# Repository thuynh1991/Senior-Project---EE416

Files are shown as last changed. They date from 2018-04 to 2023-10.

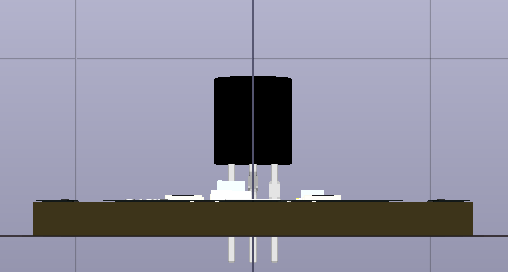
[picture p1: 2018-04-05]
Arduino_Nano_Shield_pics/3D_back.PNG

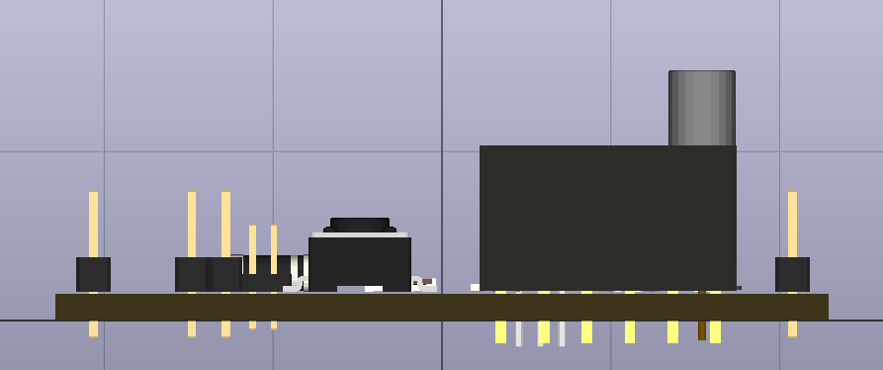
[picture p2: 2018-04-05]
Onboard System_pics/3D_back.PNG

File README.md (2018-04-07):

# Senior-Project---EE416: Leak Detection System for the Robosub Autonomous Submarine
Ensuring the protection of electronics is an integral portion of any electromechanical system. Our project goal is to protect electronics within the hull of the WSU Robosub Club’s autonomous submarine, by implementing methods of leak detection. Providing information of an onboard leak allows for preventative action, and could potentiallysave thousands of dollars worth of material onboard. We have developed a two-part procedure to check, and monitor for potential leaks. This procedure consists of testing for leaks before the submarine is submerged, and is followed by an internal system that monitors water infiltration while underway. This project has met the needs and requirements set by our clients and stakeholders, while maintaining freedom of engineering design interpretation.<br /><br />
The DS_LC234X is FTDI - USB connector and we will use atmega1284P-AU chip for the project. <br />
EE415 code: Code to test the leak before submarine is submerged. <br />
EE416 code: Code for the internal(onboard) system. <br />  
Aruino Nano Shield: is our back up plan in case the internal system is fail.

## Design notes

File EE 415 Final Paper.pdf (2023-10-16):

## Team Naura NAVSEA Robosub Alpha Prototype Results

EE 415

## December 4, 2017

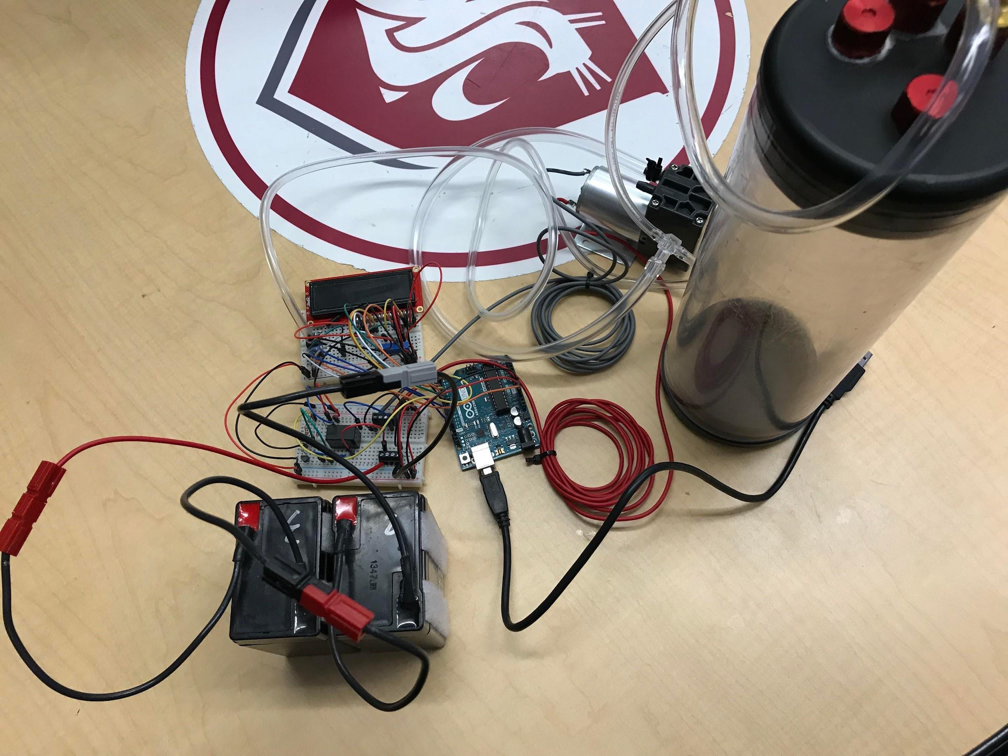
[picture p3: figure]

Mentors:
Aaron Darnton
Alex Read

Co-mentor:
Daniel Hubert

Faculty Volunteer:
Andy O’fallon

Professor:
Patrick Pedrow

Group Members:
Henderson Reaves
Nicholas Heitman
Luke Riske
Thong Huynh

Alpha Prototype Description

The objective for this semester was to develop a leak detection system for the Robosub club’s autonomous submarine, and present an alpha prototype model of the design to our industry mentors, and primary stakeholders involved. Our team followed an iterative design procedure until finally selecting a concept, and constructing the alpha prototype model. Our alpha prototype is defined as a pre-submergent leak detection system, which has been implemented by pulling a vacuum, and monitoring pressure differentials on a sealed vessel. The system is designed to require minimal human interaction, and provides clear and concise results. This scheme is standalone, and completely detached from the submarine while it is underway. Our team is confident this approach can also be useful on relative applications that need to be tested for airtightness.

Summary of Alpha Prototype Session with Industry Mentor

After introduction of ourselves, our alpha prototype model, industry mentors, and primary stakeholders to the attendees of our presentation; we began presenting on the development procedure of our alpha prototype. The following information is a summarization of the semester long iterative design process, and alpha prototype design details, which were covered in the alpha prototype presentation.

The first step in our design procedure revolved around establishment, and organization of our team. A group photo of our senior design team is shown in Figure 1, with corresponding names captioned below. The role of communication liaison for the fall semester was taken on by Nick Heitman. Our team assessed each other's strengths early on, and were able to conclude suitable roles for every member. Henderson Reaves, and Thong Huynh specialize in computer engineering, therefore, taking on tasks related with programming of the microcontroller. Luke Riske, and Nick Heitman are electrical engineers, and focused primarily on hardware design, and testing roles. Organization of tasks for each member were taken further by evaluating each other in networking, communication, research, and technical writing skills. Our team met frequently each week of the semester to update, and assess the iterative design procedure throughout the duration of EE415.

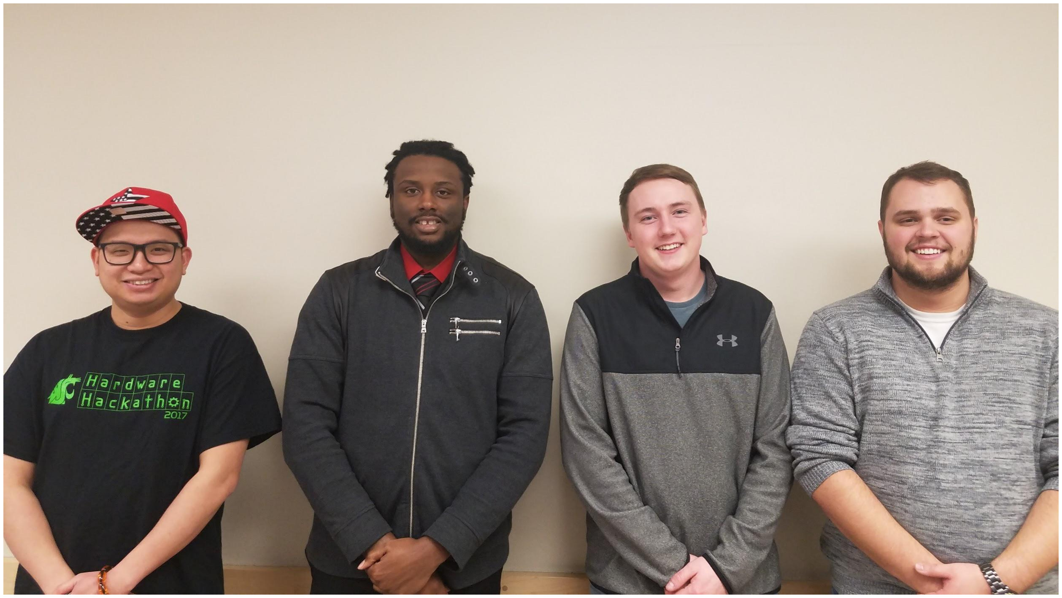
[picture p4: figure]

Figure 1. (From left to right): Thong Huynh, Henderson Reaves, Nick Heitman, and Luke Riske

It was crucial to develop an affirmative understanding of the design problem before defining goals, and specifications for our project. The abstract for the “Robosub” design problem influenced our team to interview the mentor’s from NAVSEA, and club members from Robosub to develop project needs. The summary of the problem also gave a clear indication that a pre-submersion, and internal leak detection system would be the primary focus of our design procedures. After consulting with our clients, it was clear that a water breach could damage thousands of dollars worth of electronics within the autonomous submarine, and their current method of leak detection was inefficient. Our team was able to extract needs for both systems through discussions with both parties. The information in Table 1 indicates the needs collected from meetings held with our NAVSEA mentors, and Robosub club leaders.

Table 1: Primary Needs for Pre-Submersion, and Internal Leak Detection Systems

Pre-Submersion System Needs | Internal System Needs
Minimal human interaction: Require low maintenance, and user inputs. | Send flag bit when hull is breached: Transfer data to the submarines AI system.
Display accurate and user friendly data: Show clearly whether the system is under passing or failing conditions. | Compatibility with their existing software: Must choose hardware that is programmable with their current software.
Quick results: Display test conditions in an acceptable timeframe. | Output to USB: Transfer data through their available ports.
Standalone from the AUV: Detachable, and portable system. | Meet available power requirements: Use their 12-14V onboard power supply.

The Robosub club suggested that our team keeps both systems separate, and focuses primarily on the pre-submersion system in the fall semester.

Before beginning the design phase, it is critical to work within the needs taken from clients, and stakeholders. In this situation it is the responsibility of the engineers to interpret the needs of the client into target technical specifications that can be designed around. The information contained in Table 2 shows the mapping of our clients’ needs into target technical specifications.
Table 2: Needs and Metrics with Ideal Margins
# | Need | Metrics (with ideal margins)

1 | External standalone functionality | Unit must have minimal user interfacing input, and low tolerance for data error (1 user input, 10% tolerance)
2 | Simple design | System that provides a relatively small footprint, and low maintenance (20 square centimeters)
3 | Pre-submergence check in timely manner | Check measurements, and conduct tests within a short period of time (Within 5 minutes)
4 | Meet available power specifications | Allow system to rely on independent power supply, without wall connection (12V-16V battery supply)
5 | Sampling time per measurement | Sample measurements at a fast pace (at least every 2 seconds)
6 | Accounting for changes of temperature that could be caused by internal electronics | Allow for fluctuations of temperature (2 degrees celsius)

Once, the target technical specifications were established, we had to consider the broader impacts that our design would have on surrounding systems, and the users of our design. To analyze the broader impacts we utilized the risk management technique, which was introduced by our instructor. There are 4 steps that must be followed to use this technique, which includes identifying risks, evaluating risks, making decisions, and reviewing the decisions. These steps pertain to our system design as follows in table 3.

Table 3: Risk Management technique for impact analysis

Step 1: Identify Risks | Step 2: Evaluate Risks | Step 3: Make Decision | Step 4: Review Decisions
Vacuum may drop the pressure too low | Loss: If the vacuum is overdrawn the test case could implode Probability: Low | Because it would take a very large pressure to implode the cases we moved forward with this decision | This decision was sound because controls restricting the vacuum were implemented
Board mount components may break | Loss: Components would need to be replaced Probability: Medium | Because this risk had a medium probability we continued forward with the decision but with extreme caution | This decision was questionable because we broke a leg off of the pressure sensor. Even though we fixed it.
Power supply could provide too much to the wrong place | Loss: Could cause component and system failure Probability: Low | Because we put protections in place to prevent this risk we moved forward with this decision | This decision was sound because preventative measures were taken
Numerous connections could present vulnerabilities | Loss: Could give inaccurate results Probability: Low | Because we could account for this in our tests we decided to move forward with this | This decision was sound because preventative measure were taken.

As indicated by Table 3, we were able to use the Risk Management technique to analyze the broader impacts of our system. Since these impacts were fairly low we proceeded forward with our design.

To generate concepts for the pre-submergent leak detection system we searched internally, and externally to develop possible solutions for each subsystem. The external searches included interviewing clients, and stakeholders; researching peer reviewed journal articles, searching patents, and benchmarking related products through the Thomas Register database. Some of the corresponding solutions to each subsystems are shown in Table 4.

Table 4: Concept Generation Table

Subsystems | Solution Concepts
Energy (Power) Supply | ● AC wall supply ● DC battery ● AC wall supply with rectifier circuit to convert DC ● Solar cell module ● Robosub submarine power supply ● Relay system between the “influence on vessel,” and “method of measurement subsystems” to centralize user input
Influence on Vessel | ● Removal of pressure from the vessel with vacuum generator ● Injection of pressure into the vessel with air compressor ● Injection of heat into the vessel with heating mechanism
Method of Measurement | ● Pressure measurement with pressure transducer ● Temperature measurement with temperature sensor ● Gas measurement with gas detector
Data Processing | ● PIC32 microcontroller ● Arduino based microcontroller ● FPGA ● Raspberry Pi ● Computer

In the concept selection process for the pre-submergent leak detection system, we evaluated each possible solution generated for each subsystem. Taking the Robosub club’s previous method of leak detection into account, which involved pulling a vacuum, and analyzing pressure differentials with an analog pressure gauge, we decided to follow a similar method by using a pressure sensor controlled with an arduino microcontroller. Since the design needed to be mobile, our team also concluded that a battery supply should be used to power our system. Addition of a relay was also considered to minimize human interaction, and add a safety element to our design. Table 5 shows the concept selection for our design.

Table 5: Concept Selection Table

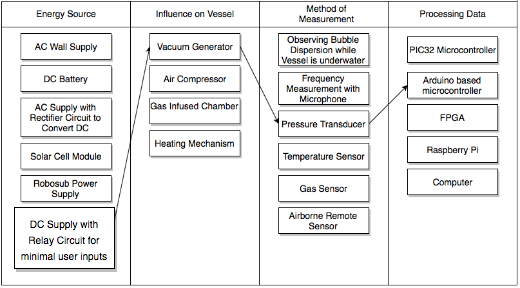
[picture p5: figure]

The initial hardware design we envisioned is shown in Figure 2, which involved connecting the microcontroller, and pressure sensor between the testing chamber with tubing. Turning on the vacuum generator would bring the combined volume to the same pressure level. Once the correct pressure level is reached the vacuum generator would be turned off by the relay, and the pressure sensor measures the pressure within the test chamber to make sure there is no major pressure deviations in a short timespan.

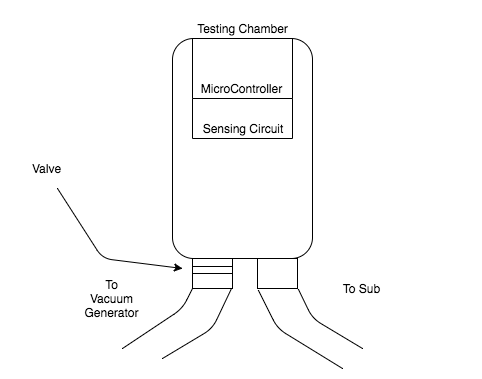
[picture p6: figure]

Figure 2. First Concept for the Pre-Submersion System

After looking further into our design, and pondering its abilities, we decided that the model was too bulky for transportion. The design was reconsidered to what is shown in Fig. 3, which consists of a ported pressure sensor connected directly with the vessel, and vacuum through tubing. This not only simplified the design, but allowed for the test chamber to simulate the submarine for the alpha prototype.

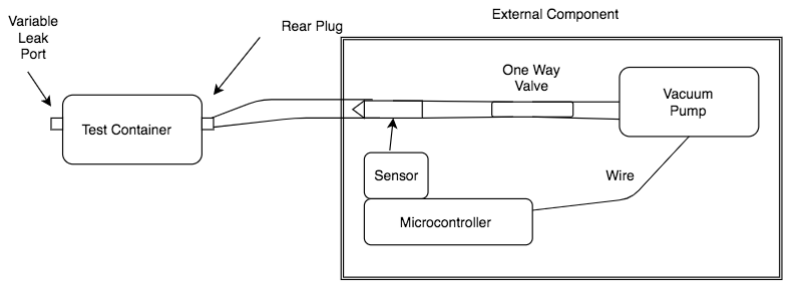
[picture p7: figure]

Figure 3. Second Concept for the Pre-Submersion System

Before our design could be built, we were obligated to contact the EHS regarding the safety of pulling a vacuum on a sealed vessel. We were assigned to complete a job hazard assessment EHS assistant director Shawn Ringo. The assessment was meant to identify potential hazards, appropriate controls, and personal protective equipment. Shortly after submission we were informed that our job hazard assessment was acceptable for the design.

The Arduino UNO microcontroller was borrowed from the Robosub club for this design, and is used for interfacing each of the subsystems within the pre-submergent leak detection system. The UNO serves as a placeholder in our alpha prototype for a printed circuit board in the future. After extensive research we determined the HSC differential pressure sensor with SPI protocol would be appropriate for our task. The particular HSC sensor we chose references atmospheric pressure, and uses a ported hose connection to analyze pressure differences from the referral. We were able to utilize a 12V vacuum generator, and two 6V batteries that were in the Robosub clubs inventory. The test capsule used in the alpha prototype presentation is a recycled battery case previously used on the autonomous submarine.

The schematic in Figure 4 shows an overview of the alpha prototype design, which was created with the Fritzing software application. The schematic is rough, in the sense of correctness of specific components, and wire coloring, but it is a good representation of the electronics used in the design. Four subsystems are controlled by the Arduino UNO microcontroller including the LCD display, pressure sensor, BJT switch, and relay coil. The pressure sensor shown in the schematic comes from a different family of sensors, but utilizes the same pin layout, and SPI protocol of our HSC sensor. It should also be noted that the potentiometer used in the schematic is much a larger representation than the10kΩ sliding potentiometer used in the physical design.

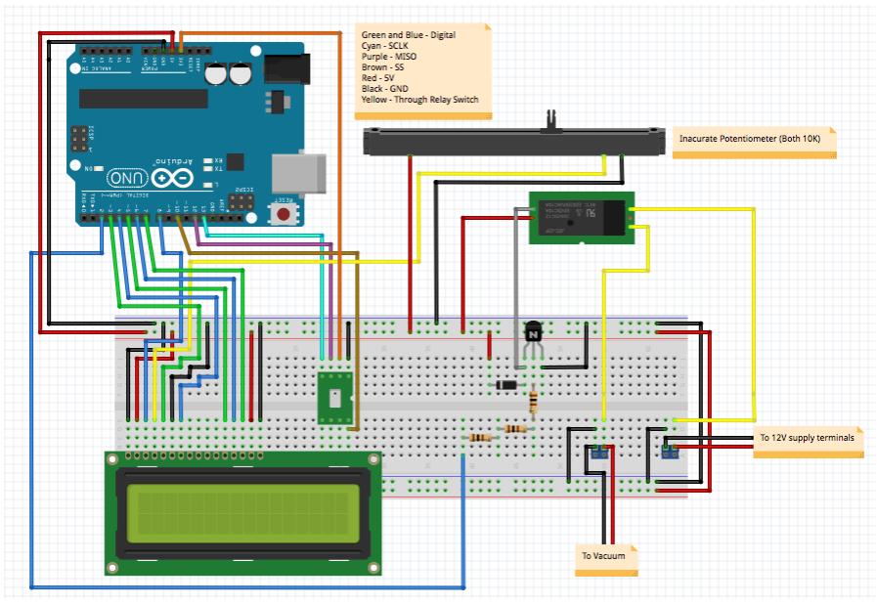
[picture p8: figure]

Figure 4. Electrical Schematic of the Alpha Prototype Design

The circuit in Figure 5 shows the relay, which is controlled by a bipolar junction transistor (BJT). The relay coil is connected to the 5V Vcc pin on the Arduino UNO, and is capable of

200mA of current. The collector of the BJT is connected to the opposite polarity of the relay coil, and is used as a switch to control the current flow. The base of the BJT is connected to a 5V digital pin on the microcontroller, which is capable of 20mA of current. From the datasheet of the BJT, it was determined that the ratio of collector, and base current needed to be greater than 10 for saturation (Amplifier Transistors [APA], n.d.). Making the assumption that the relay coil has low resistance under DC conditions, a base current of 15mA, and a 0.7V diode voltage drop from the collector to the emitter, the base resistor was solved as 286.7Ω with a simple KVL loop. In the construction of the physical circuit, three 100Ω resistors were placed in series at the base of the BJT. The diode in Fig. 5 is configured for a safe path to allow current to flow when the BJT is turned off, and current is induced by the change in magnetic field from the coil.

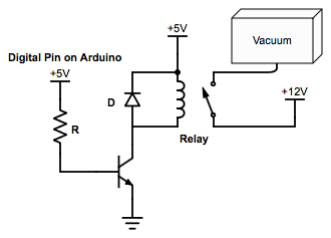
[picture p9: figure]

Figure 5. Relay Controlled with a BJT

In order to use our microcontroller (MCU) system, we used Arduino Integrated Development Environment (IDE) software to program the board. Our board has to be Arduino compatible since the robosub club is using Arduino for the Autonomous Underwater Vehicle (AUV). Arduino is an open source platform that is used to build electronic projects. It can be used in different platforms like Windows, Macintosh OSX, and Linux operating systems. We can use programmable circuit board (or microcontroller) with IDE software to upload our code to the physical board. For the pre-submersion test, we use Arduino UNO board and programmed it with C language. A schematic of the Arduino UNO is shown in Figure 6 (What is an Arduino?, 2013).

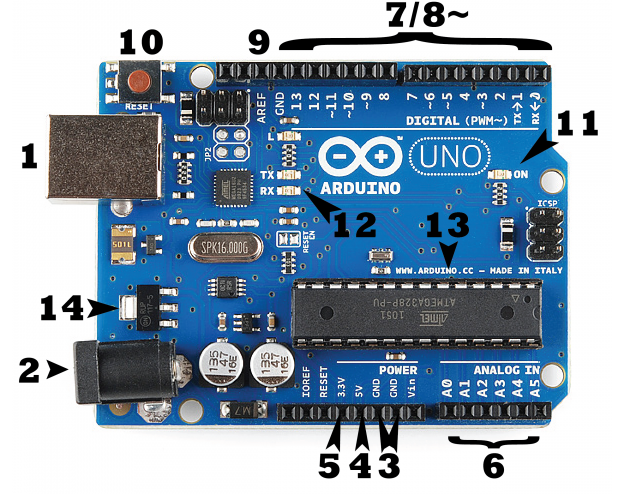
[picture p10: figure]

Figure 6. Arduino Uno

The following correspond with the numbers on the Arduino UNO shown in Fig. 6:
- Number 2: Power Jack (Use to connect to independent power source)
- Number 1: USB port
- Number 3: Ground
- Number 4,5: Voltage Supply (3.3V and 5V) for other components.
- Number 6: Analog input signal (Use for Analog sensor).
- Number 7: Digital input/output signal
- Number 8: Pulse-width modulation (PWM) input. It can use for digital pin, but every pin with (~) before them, they can also be used for PWM input signal
- Number 9: Analog Reference. It is used to set external reference voltage (0 - 5V)
- Number 10: Reset button. It is used to reset the board.
- Number 11: Power LED. It is used to indicate that the board is On or Off

- Number 12: TX (transmitter) and RX (Receiver) LED. Indicating the communication between RX and TX.
- Number 13: It is Integrated Circuit (IC). It is a AVR microcontroller and a main controller of the Arduino board. The microcontroller is designed by Atmel company. Different Arduino board will have different microcontroller.

In addition, we use Serial Peripheral Interface (SPI) bus system for the communication between our MCU and sensor. By using the SPI bus system, we can avoid problems with the system clock since the MCU, and sensor have their own clock rates. In the SPI bus system the clock signal, and data signal are sent from the MCU to the sensor separately. This is so the sensor will be able to receive correct data from the MCU since they are running on the same clock system. Moreover, there are two modes for the SPI bus system. The first mode is full-duplex mode, where the MCU receive, and send data to the sensor. The other is half-duplex mode, which is shown in Figure 7. In this mode, the MCU can only receive the data from sensor. The UNO board has a support library for SPI system (A Brief Introduction to the Serial Peripheral Interface (SPI) [APA], n.d.). The half-duplex mode was used for our project, which allows two outputs from the MCU, and one input from the sensor. The first output is Serial Clock (SCLK). The SCLK is the clock signal which is generated by the MCU and it is for the data transmission. The second output is Slave Select (SS) which is used to activate the sensor. The input MISO (Master In/Slave Out) is the sensor line for sending data to Microcontroller (SPI Communication with Honeywell Digital Output Pressure Sensors, 2012).

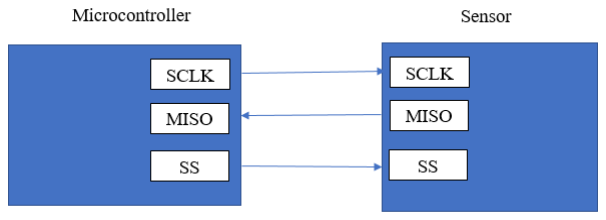
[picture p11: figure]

Figure 7. Half Duplex Mode of the SPI Bus System Moreover, the MCU will use the Slave Select (SS) line to activate the sensor, and it will also generate the clock signal (SCK) for the sensor. Then the sensor will send data back to the

MCU based on each clock pulse from MCU. In addition, the connection pins on the Arduino UNO board for SCLK, MISO, and SS line are 13, 12, 10 respectively. Thus, in order to activate the sensor, we set pin 10 to LOW by writing:

uint8_t SS_pin = 10; // Assign pin for SS line
pinMode(SS_pin, OUTPUT); // Initialize the SS pin as output
digitalWrite(SS_pin, LOW); // Set the digital SS pin low

When the pin of SS line is activated, the MCU will generate a clock signal and send it to sensor via pin 13. When the sensor receive clock signal from MCU, it will send back the pressure data via pin 12. At this point, we wrote a function to read the data from sensor:

int16_t Sensor_reading (int8_t SS_pin)
{
SPI.beginTransaction(SPISettings(800000, MSBFIRST, SPI_MODE1)); // 800KHz digitalWrite(SS_pin, LOW);

int Byte1 = SPI.transfer(0x00); // Read first pressure sensor byte
int Byte2 = SPI.transfer(0x00); // Read second pressure sensor byte

digitalWrite(SS_pin, HIGH); // Deactivate sensor by setting SS line high SPI.endTransaction();

int16_t sensor_output = Byte1 << 8 | Byte2; //Required for shifting first byte left
return sensor_output; //Return output pressure reading
}

The HSC differential sensor transmit up to 4 bytes of data. The first two bytes contain pressure data, and the last two bytes is optional for temperature. We only use the first two bytes of the sensor in this project. The data read the sensor is shifted in Most Significant Bit (MSB), and it is captured at falling edge of clock pulse. Thus, the output data will be sent to the MCU at rising edge of clock pulse, and the clock phase (CPHA) is 1. The value of clock polarity (CPOL) of our sensor is zero since the clock is at idle when low (SPI Communication with Honeywell Digital Output Pressure Sensors, 2012). Also, the clock frequency of our sensor is from 50 to 800 kHz (SPI Communication with Honeywell Digital Output Pressure Sensors, 2012). Thus, we initialized the sensor settings for the SPI system before activating the sensor to read data with the following code:

SPI.beginTransaction(SPISettings(800000, MSBFIRST, SPI_MODE1)); //800KHz

The “SPI_MODE1” is used to set the mode of our sensor in SPI library system based on the CPHA and CPOL.

Moreover, We used pin 3, 4, 5, 6, 7, 8 to display the digital output on our LCD screen. The <LiquidCrystal.h> library was used to interface our 16x2 LCD screen. To use the LCD screen on the UNO board we just needed to declare the pin numbers used to connect the LCD in our code, and use the “lcd.print” command to display the output on the screen. We also use “lcd.setCursor(x,y)” to set the position of the output on the LCD screen.

In addition, We used pin 2 on UNO board to control the BJT transistor that controls the relay for our vacuum. We physically connected the base of the BJT to pin 2 on the UNO board, and set pin 2 as an output pin by using “pinMode(2, OUTPUT);” command. After that, we use “digitalWrite(2, HIGH);” command to set the pin to high, and allow for current to flow through the relay coil. Finally, we applied an algorithm to control the relay when we reached a pressure 0.9ATM. We also used the Arduino Serial Plotter to graph our result in real time. The Serial Plotter is a built in application, and it takes incoming data via USB port and graph them on X/Y axis. An example of the Serial Plotter is shown in Figure 8. The Y scale is generated based on our final valued and the X axis has 500 points and each tick is equal to one “Serial.println()” command (New Arduino Serial Plotter, 2015).

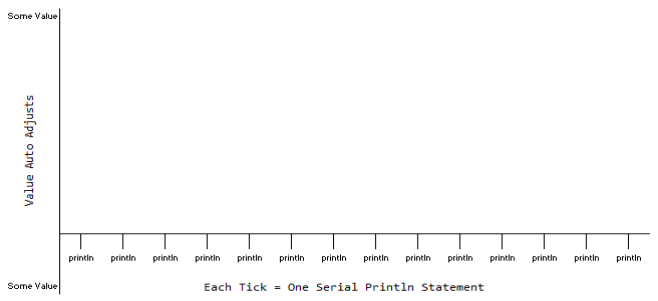
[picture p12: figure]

Figure 8. Arduino Serial Plotter

Following the construction of the alpha prototype, we began conducting tests to make sure our design functioned properly. These tests consisted of five trials over a duration of two minutes each. The pressure was taken down to an initial stage of 0.9 ATM, which was approved by our contact at the EHS, and then fluctuations of the pressure in our system were observed. The results of these tests are summarized in Table 4.

Table 4: Pre-submergent leak detection operation test results

Time | Initial Pressure | Final Pressure | Difference
2 minutes | 0.9 ATM | 0.92 ATM | 0.02 ATM
2 minutes | 0.91 ATM | 0.92 ATM | 0.01 ATM
2 minutes | 0.9 ATM | 0.92 ATM | 0.02 ATM
2 minutes | 0.91 ATM | 0.93 ATM | 0.02 ATM
2 minutes | 0.91 ATM | 0.92 ATM | 0.01 ATM

Because the average difference was 0.016 ATM, and the standard deviation was 0.005477, we were able to consider a passing condition of less than 0.93 ATM, and a failing condition greater than 0.935 ATM. These conditions were integrated into our code by using a flag variable to indicate whether or not the pressure rose above 0.935 ATM, a delay cycle to make sure that the test runs for 2 minutes while checking if the flag is triggered, and a pass/fail output that indicates on the LCD if the test passed or failed.

Design Modifications Resulting from Alpha Prototype Activities

After troubleshooting hardware, software, and test logic, our alpha prototype performed as anticipated. However, once we presented our design to our clients and stakeholders, we were informed of some changes that we could make to benefit its functionality. One example would be dropping the pressure down to 0.5 ATM instead of our approved value of 0.9 ATM because this corresponds with the pressure that the sealed vessel would experience at 15 feet below water. We didn’t consider the pressure level as it relates to depth because the system would be above water when the test is conducted but it makes sense to bring it down to a level that would actually be experienced by the sub. Another modification to our design is finding another way to display the pressure data because of footprint considerations. The LCD that we are using is quite large in comparison to what our PCB will be once it is refined. Therefore if we want to get it as small and as light as possible we should consider a new display method. The final modification that was suggested to us is to use a MOSFET to replace the relay that controls when the vacuum turns on and off as this would also reduce the size of the final system and simplify the design.

Overall, these changes are minor and can be easily implemented. There were no major design changes that we experienced while creating our alpha prototype. This can be attributed to our concept generation and selection stages of our design procedure, and the collaboration we did with the Robosub Club in the final weeks of the semester.

Future Iterative Design Activities (Plans) for EE416

In EE416 we plan to advance the pre-submergent leak detection system into the beta prototype stage. In the following semester we plan to immediately test our design on the largest volume of the Robosub club’s AUV. This will conclude if our vacuum generator is powerful enough to keep for our system. We also plan to add an independent supply for the microcontroller, and implement switches to initiate the test. A MOSFET will be considered to replace the relay in the system, and seven segment displays might replace the LCD to condense the footprint of the electronics.

The current alpha prototype performs the desired tasks although, it can be condensed, and organized. We plan on shifting our breadboard design to a PCB, and using KiCad for design, and OSHPark for manufacturing. While the PCB is being manufactured we plan to find a smaller 12V power supply for our vacuum. Having a smaller power supply will decrease the overall size, and provide ease of transportation for the system. We can then begin to design the parcel for transporting the system. We plan to use the ATmega2560 AVR microcontroller to for our PCB, which is the standard on most of the boards produced by the Robosub club. The Random Access Memory (RAM) of ATmega2560 microcontroller has 8 KB (Atmel ATmega640/V-1280/V-1281/V-2560/V-2561/V [APA], n.d.), and should run smoothly with our software.

To complete the onboard leak detection system, we will resume the iterative design process started in the beginning of fall semester. We will meet with our clients to refresh on the concept we plan to implement. We will present our generated concepts, and new concerns that develop. We currently plan on implementing the onboard model with either conductive leads, or a water detector attached at the bottom of the AUV. The system will send a signal from our microcontroller to the submarine’s CPU if water is detected. It is crucial that we work on this task in parallel with the pre-submersion system to ensure both systems are complete by the end of EE416.

Discussion

Our team believes we were successful in creating a physical alpha prototype that is representative of what our instructor and clients approved. Although there is need for optimization, as is in most alpha prototypes, we feel that we have made good progress towards our goal of designing a system to solve our client's problem. Because of this achievement, we think that we have progressed as a strong team, and were able to utilize everyone’s strengths to our advantage. We also involved our industry mentors, faculty advisor, and the robosub club to help us get to this point. It is a combination of these factors that will continue to push us towards our goals in EE416.

Conclusion

In conclusion, the demonstration of the pre-submersion alpha prototype system was a success. The design successfully measured the internal pressure of a sealed vessel, and identified whether leak was present. The alpha prototype also plotted live pressure differentials, and displayed the testing state on an LCD screen. We designed this system to be standalone, and require minimal user input. Despite a few components, and parameters that will be tweaked, the design met the desired expectations. We have a plan for advancing our alpha prototype design, as well as our onboard system in the future. Our design team will be focused on completing the necessary tasks immediately to remain on schedule in the following semester.

Appendix

Gantt chart for EE416:

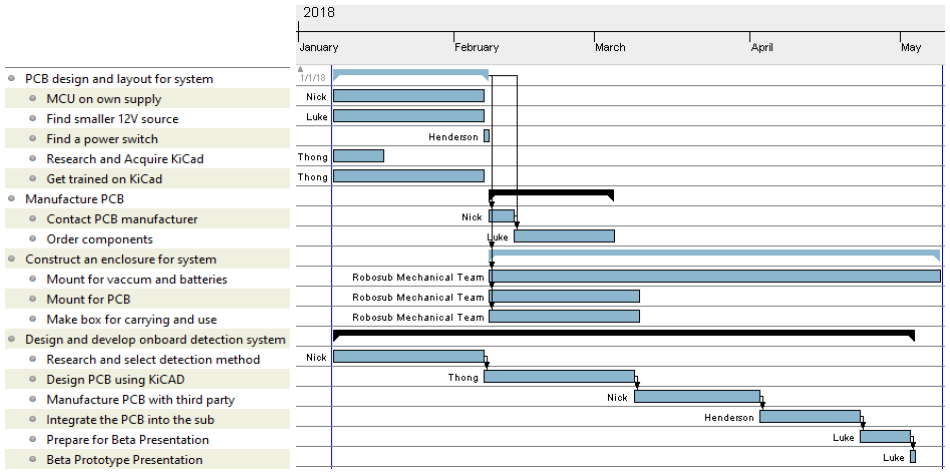
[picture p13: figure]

Bibliography:

What is an Arduino? (2013, February 26). Retrieved December 08, 2017, from https://learn.sparkfun.com/tutorials/what-is-an-arduino

A Brief Introduction to the Serial Peripheral Interface (SPI). (n.d.). Retrieved December 8, 2017, from https://www.arduino.cc/en/Reference/SPI

SPI Communication with Honeywell Digital Output Pressure Sensors. (2012, May). Retrieved December 8, 2017, from https://sensing.honeywell.com/index.php?ci_id=45843

New Arduino Serial Plotter. (2015, November 4). Retrieved December 08, 2017, from https://rheingoldheavy.com/new-arduino-serial-plotter/

Atmel ATmega640/V-1280/V-1281/V-2560/V-2561/V. (n.d). Retrieved December 8, 2017, from http://www.atmel.com/Images/Atmel-2549-8-bit-AVR-Microcontroller-ATmega640-1280-1281-2560-2561_datasheet.pdf (http://www.atmel.com/Images/Atmel-2549-8-bit-AVR-Microcontroller-ATmega640-1280-1281-2560-2561_datasheet.pdf)

Amplifier Transistors. (n.d). Retrieved December 8, 2017, from https://www.onsemi.com/pub/Collateral/P2N2222A-D.PDF

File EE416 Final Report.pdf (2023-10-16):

### NAVSEA Robosub EE 416 Final Report Team Naura April 15, 2018

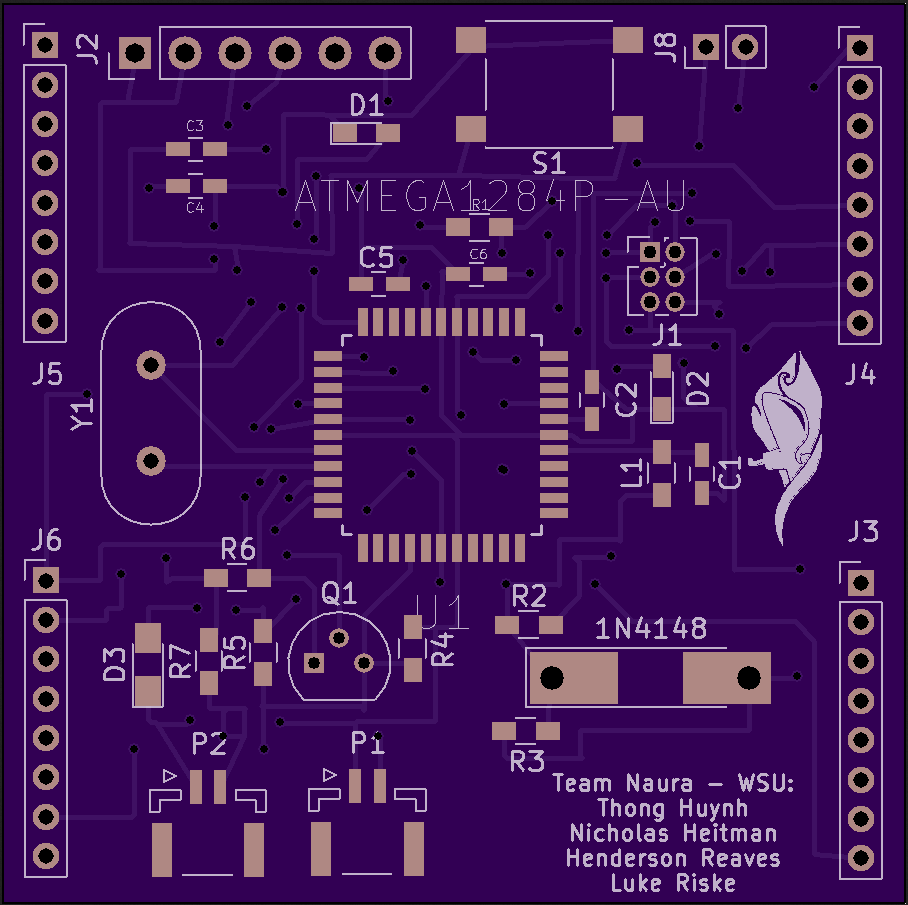
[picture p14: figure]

Mentors:
Aaron Darnton
Alex Read

Co-mentor:
Daniel Hubert

Faculty Volunteer:
Andy O’fallon

Professor:
Patrick Pedrow

Group Members:
Henderson Reaves
Nicholas Heitman
Luke Riske
Thong Huynh

Table of Contents

Executive Summary | 2
Introduction |
.2

Description of Culminating
Design | 3

Project
Management | 4
Results |
5

Broader Impacts and Contemporary
Issues | 6

Limitations and
Recommendations | 28

Conclusions and Future
Work | 30
Acknowledgements | 31
References | 31
Appendixes | 32

Executive Summary

This report covers the design process used by the EE416 Senior Design Team, Team Naura, to

create a leak detection system for the Autonomous Submarine created by the WSU Robosub

Club, sponsored by NAVSEA. Per the Robosub Club’s requirements, the leak detection system

was to use a modular approach: One system for detecting leaks prior to submersion, and one

system for detecting leaks onboard the submarine during operation. For the EE415 fall semester,

our Team brought the pre-submersion module to an alpha prototype level. The objective of the

EE416 semester was to bring the pre-submersion module to a beta prototype level and the

onboard module to an operational alpha prototype level, of which both objectives were met.

Details of both designs, the results to date, broader impact considerations, and conclusions made

throughout the process are also described. All external resources used throughout this process

have been cited and are included in the reference page.

Introduction

To detect leaks within the autonomous submarine prior to submersion, air pressure was utilized.

The design would connect to the subject test vessel and create a sealed apparatus and then use

a vacuum pump to reduce the air pressure within the system. Because air pressure is naturally

maintained at a level of one atmosphere, the air pressure within the sealed apparatus would try

to rise back up to atmospheric pressure. If it was able to successfully rise back to one atmosphere

within a certain time constant, that would mean there is a leak in the system that needs to be

investigated. Otherwise, the air pressure would remain at the level that the vacuum was shut off

at.

To detect leaks within the autonomous submarine during operation, a water sensor would be

used. This water sensor was created by Blue Robotics and functions by using an absorbent

sponge material that expands upon contact with water and sends an analog signal. This analog

signal would then be processed by our design into a usable digital signal that would be sent to

the autonomous submarine to indicate if a water leak has been detected.

Therefore, transitioning into this semester, our team’s objective was to bring the pre-submersion

module into a beta level prototype. This included moving our alpha prototype, which was a

breadboard circuit, onto a printed circuit board and creating an enclosure to make it more usable

by the club. The goal for the onboard system was to get an operating alpha prototype. This meant creating and testing a breadboard circuit and then transitioning that circuit onto a printed circuit

board to be integrated onto the submarine.

Description of Culminating Design

The design for the pre-submersion module consists of a PCB interface shield for the Arduino UNO

microcontroller. This system is used to test the airtightness of the Robosub autonomous

submarine before being submerged. This test consists of pulling a vacuum on the submarine to

a threshold of 0.9ATM, monitoring pressure deviations over time, and providing results dependent

on total pressure deviation. The design features its own portable case that encloses the vacuum

pump, and electronic components needed to perform the pressure test. A vacuum hose that

connects to the vent plugs of the submarine, and a wall outlet plug are easily accessible from the

outside of the case. This final design is ready for use by the Robosub Club and will perform as

intended.

The onboard leak detection system has been developed exclusively throughout the course of

EE416. This system consists of a PCB controlled with the atmega1284P microcontroller, and SOS

probes provided by Blue Robotics. The objective of this design is to detect water leaks onboard

the submarine by monitoring the SOS probes and send a flag bit to the sub’s CPU in an instance

of a leak. When the system is fully integrated into the submarine, two probes will be placed on

each end of the center bulkhead. This will provide enough reliability to detect water infiltration,

because the submarine only experiences minor changes of pitch during movement underwater.

This PCB is also setup to provide the Robosub club with more functionality from the

microcontroller if need be, which includes: ADC (Analog Digital Conversion) inputs, temperature

measurement, PWM outputs, and more.The dimensions of the onboard leak detection PCB are

oriented to meet the specifications provided from Robosub club members.

Because of component arrival times, and inexperience with programming a blank microcontroller,

a backup plan has been set in place to ensure a beta prototype is presented for the onboard

system. The backup plan consists of a shield design for the Arduino NANO microcontroller to

operate with the Blue Robotics SOS probes. The NANO shield is designed to meet all general

requirements of the PCB created with the atmega1284P microcontroller but lacks the extra

functionalities that the Robosub club could use for additional projects. The NANO shield PCB is

less expensive than the one created with the atmega1284P and offers a smaller footprint. The only downfall to this backup plan is that it is specifically made for water leak detection onboard

and will not provide the extra I/O pins.

Project Management

Before beginning work on the project, our team decided that it would be best if we had a team

member keep track of the project schedule that we all agreed to. This team member would have

the role of Team Lead and would be responsible for adhering to the project schedule and making

sure the other team members had the necessary support. This is the primary method for

managing our project. The secondary method was to have each team member hold each other

accountable for completing tasks assigned to them. This secondary method would assist the

Team Lead to ensure the success of the primary method for meeting project deadlines. Once the

role of Team Lead was assigned each team member contributed to the creation of a project

schedule shown in Figure 1. This project schedule indicated tasks for each member to complete

and a timeframe to complete it in. Upcoming tasks would be identified with a blue bar while current

tasks or tasks in progress would be indicated by a yellow bar. Once tasks were completed they

were changed by the Team Lead to be a green bar. Should tasks extend beyond the given time

frames, they would have been changed to a red bar which would prompt the Team Lead to contact

or meet with the team members to discuss the best course of action. Finally, the vertical blue bars

indicated the beginning and end of the semester and the vertical red bar indicated what day it was

currently, or rather. This red bar helped the Team Lead and the other team members keep track

of what is currently being worked on.

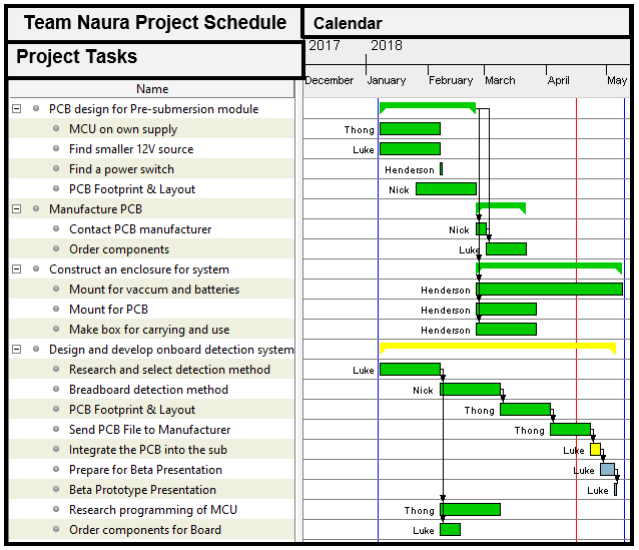
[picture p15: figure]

Fig 1. Project Schedule used by Team Naura for the EE416 Spring Semester

Results

Both onboard, and pre-submersion PCBs were modeled with KiCad EDA software. KiCad is an

open source software suite for Electronic Design Automation (EDA). The program handles

Schematic Capture, and PCB Layout with Gerber output. The suite runs on Windows, Linux and

Mac OSX and is licensed under GNU GPL v3.

The pre-submersion leak detection system PCB is designed as a shield for the Arduino UNO

microcontroller. The design consists of a 16x2 LCD display, BJT controlled vacuum relay circuit,

and Honeywell HSCDAND015PDSA3 pressure sensor. All components are powered with a

5.5mm, and 2.1mm center pole diameter barrel jack that supplies a maximum of 24W. The

schematic of the shield design is modeled in Figure 2, which exhibits all necessary connections

for the PCB. The JZC-11F relay controls the operation of a 12V vacuum generator and can easily

be turned on with manipulation of the base pin (D2) of the BJT. The Serial Peripheral Interface

(SPI) pins of the UNO microcontroller are used to control the Honeywell pressure sensor, which

is set to transmit data at a rate of 9600 bits per second. A 10 kΩpotentiometer is used to change

the brightness settings of the 16x2 LCD screen that displays live data while testing is underway.

This LCD screen accounts for most of the digital pin connections (D8, D7, D6, D5, D4, D3) that

are shown in the schematic.

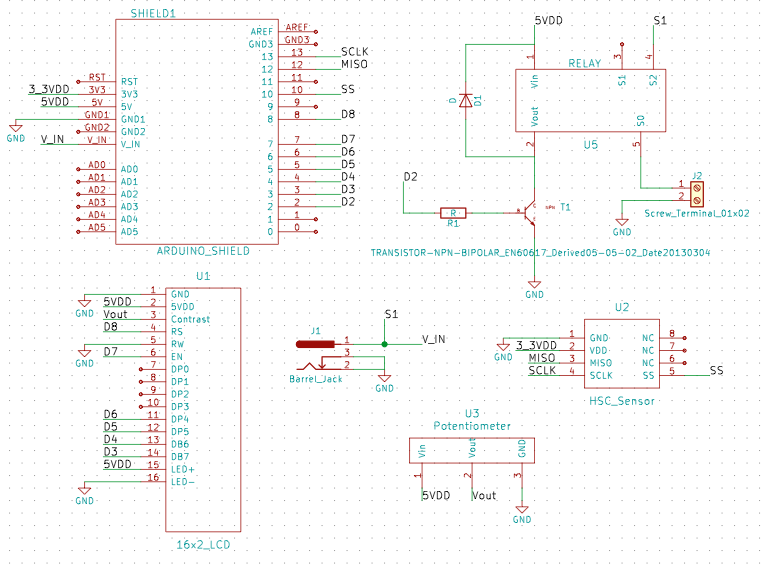
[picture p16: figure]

Fig. 2 Schematic for Pre-Submersion Pressure Testing System

The PCB layout for the pre-submergent system is shown in Figure 2, and has dimensions of 70.61

mm x 56.14 mm. This layout follows design rules provided by the manufacturer OSH Park. Most

of the trace widths for this design are 0.300mm, with the exception of the connection made from the barrel jack to the vacuum generator, which is 1.000mm. The large trace is to account for 0.53A

of current that was measured between our 12V supply, and the vacuum with the breadboard

circuit model of the design. The red traces correspond with connections made on the front copper

layer, and green traces correspond with ground connections on the back copper layer of the

board. No conductor vias were needed for this PCB layout. Each of the outer pins on the PCB

layout are soldered with male pin headers, which fit directly into the Arduino UNO. The barrel jack

splits power between the microcontroller, and vacuum generator. This layout is what will be

presented at the beta prototype poster session, which is in Rev. 0. Since receiving and testing

the PCB, minor revisions have been made to the layout in case the Robosub club needs to reprint

the PCB in the future. The reasons for these revisions have been assessed, and are included in

the “Limitations and Recommendations” portion of this document.

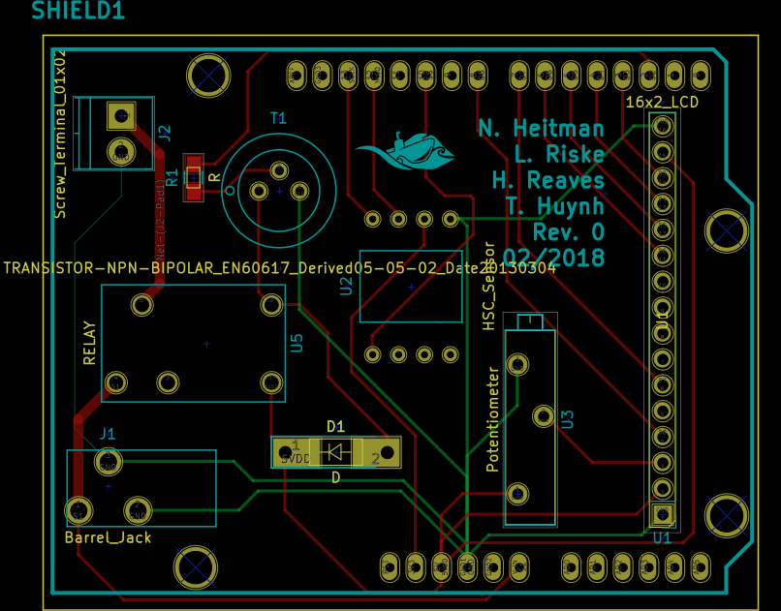
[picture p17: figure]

Fig. 3 Layout for Pre-Submersion Pressure Testing System

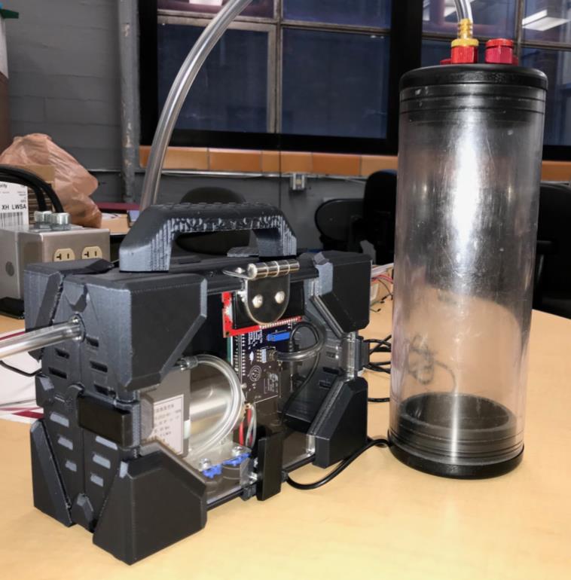
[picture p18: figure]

Fig. 4 The Testing Case for Pre-Submersion Pressure Testing System

The functionality of the pre-submersion system has been validated with a testing chamber, and

the Robosub club’s autonomous submarine itself. The testing procedure consists of attaching the

vacuum hose to the vent plug located on the vessel being tested, before plugging the system into

the wall. A short delay should occur before the vacuum turns on, and the LCD starts displaying

data. Once the internal pressure of the vessel being tested reaches 0.9ATM, the vacuum

generator will turn off. For two minutes the LCD screen will print the live pressure data in ATM,

and be in “TESTING” mode. After the two minutes pass the LCD will either display “PASS,” or

“FAIL.” The “PASS” condition occurs if the internal pressure does not rise more than 0.15ATM,

from the initial 0.9ATM threshold. This indicates that the vessel contains no major leaks before

being released underwater. The code for this system has been written in Arduino, which is an

open source programming software. Robosub club members have full access to the code, and

are capable of changing the pressure threshold, testing condition, and duration if needed. Data

has been obtained with the pre-submersion beta prototype to determine the length of vacuum

operation, and deviation of pressure from initial threshold for both vessels. The results in Table 1

show the data for both the Robosub, and testing chamber vessels.

Table 1 Pre-submersion Pressure Testing System Performance on Testing Chamber, and

Robosub Autonomous Submarine

Testing Chamber | Robosub Autonomous Submarine
Vacuum Operation | Initial Pressure | Final Pressure | Vacuum Operation | Initial Pressure | Final Pressure
4.28 s | 0.89 ATM | 0.91 ATM | 48.7 s | 0.89 ATM | 0.90 ATM
3.44 s | 0.90 ATM | 0.91 ATM | 45.9 s | 0.90 ATM | 0.90 ATM
3.68 s | 0.90 ATM | 0.91 ATM | 43.8 s | 0.90 ATM | 0.90 ATM
3.52 s | 0.90 ATM | 0.91 ATM | 45.8 s | 0.90 ATM | 0.90 ATM

The tests were run for two minutes after reaching the initial pressure threshold. The Robosub autonomous submarine has a volume of approximately 0.02512m³ without subtracting the

internal electronics, while the testing chamber has a volume of 0.002059m³

The onboard leak detection system is designed with the atmega1284P-AU chip and SOS Leak

Sensor to detect water quickly and reliably, before any major damage can occur. The schematic

of the onboard system is shown in Figure 5.

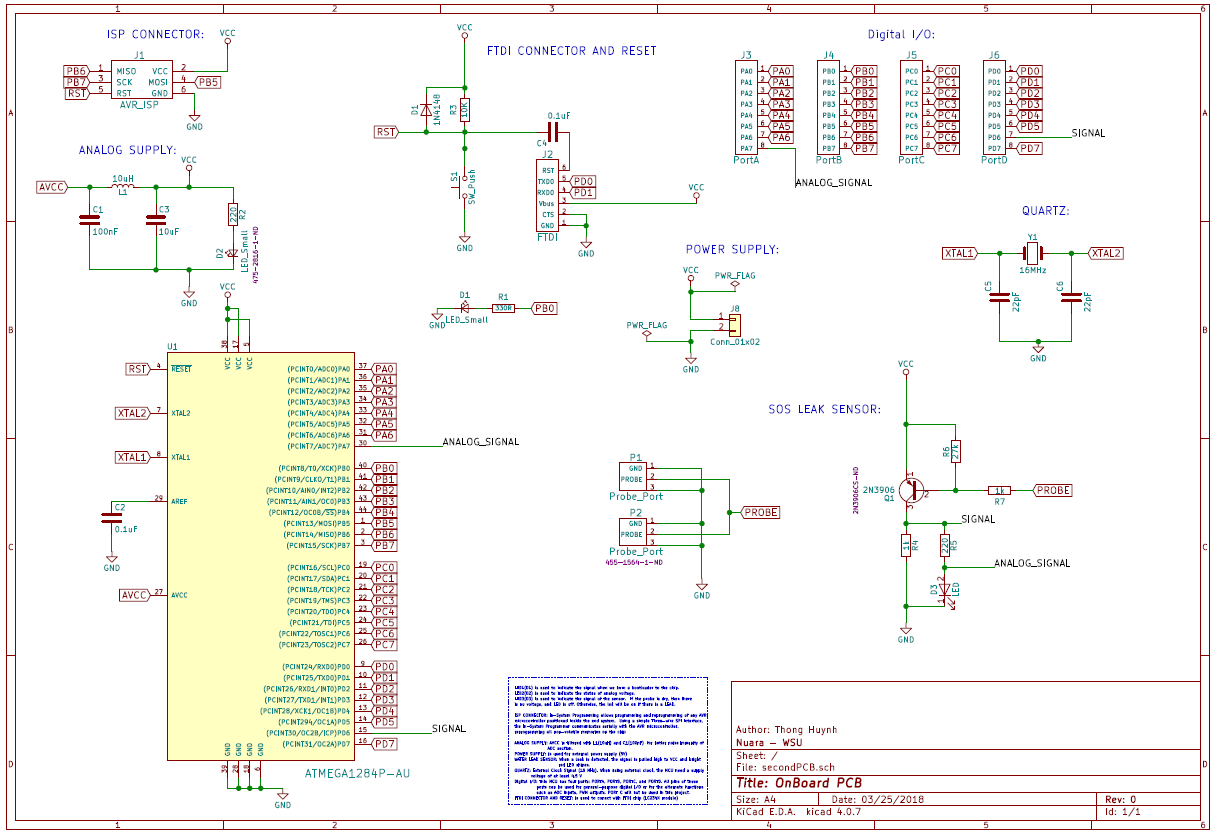
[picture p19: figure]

Fig 5. The Onboard System Schematic

The ATmega1284P microcontroller is the MCU (Microcontroller Unit) used in the onboard system

as a main controller. It is a low-power CMOS 8-bit microcontroller based on the AVR enhanced

RISC architecture. Its data-bus architecture and internal registers are designed to handle 8

parallel data signals. The chip has three types of memory:

- Flash Memory: 128KB non-volatile memory combine with read-while-write capabilities. It

is used to store applications on the chip.

- SRAM Memory: 16KB non-volatile memory. It has a larger SRAM memory compare to

other microcontrollers. This is used for storing variables used by the application while it's

running.

- EEPROM Memory: 4KB non-volatile memory. It is used to store data that is available

even after the board is powered down and then powered up again.

The On-chip ISP Flash allows the program memory to be reprogrammed In-System through an

SPI serial interface, by a conventional nonvolatile memory programmer, or by an On-chip Boot

program running on the AVR core [1].

- ISP (In System Programing) connector: In-System Programing allows programming

and reprogramming of any AVR microcontroller positioned inside the end system. Using

simple three wire SPI interface, the In-System Programing communicates serially with the

AVR microcontroller, re-programming all non-volatile memories on the chip.

- FTDI (Future Technology Devices International) connector: 6-pin connector with the

following pinout: RTS, RX, TX, 5V, CTS, GND. This is used to power our board and

transfer the data to the main CPU on the sub.

- Analog Supply: Analog power supply from the microcontroller. AVCC is filtered with

L1(10uH) and C1(100nF) for better noise immunity of ADC section. The decoupling

capacitor C3(10uF) is placed as close as possible to the power supply.

- External Power Supply: 5V external power supply.
- Digital I/O: This MCU has four ports: Port A, Port B, Port C and Port D. All pin of these

ports can be used for general – purpose digital I/O or the alternate functions such as ADC

inputs, PWM outputs. Port C will not be used in this project.

- Quartz: External clock signal (16Mhz). When using the external clock signal, the MCU

need a supply voltage at least 4.5V

- SOS Leak Sensor: It is used to detect the water infiltration. The probe is connected with

a PNP transistor (2N3906), VCC (5V) and GND through some resistors. When a leak is

detected, the signal is pulled high to VCC and bright red LED (D3) shines. The circuit that

reads from the SOS Leak Sensor is borrowed from Blue Robotics. [2]

- LEDs: The LED1(D1) is used to indicate the signal when we burn a bootloader to the chip.

The LED2(D2) is used to indicate the status of the analog voltage, and the LED3(D3) is

used to indicate the signal of the SOS Leak Sensor.

- Signals: The digital signal is connected to pin PD6 on the chip to send the message to

the main CPU when there is a leak via using digital data. In addition, the analog signal can

also be used and more accurate than the digital signal to detect a leak and send the

message to the CPU. The analog signal is connected to pin PA7 on the chip and it will be

required of using ADC for analog signal.

Many considerations were made in the design process for PCB (Print Circuit Board) layout. These

considerations include the dimensions of each component (footprints), dimension of the board (it

needs to fit within the actual dimensions on the sub), connections between each component on

the PCB, and much more. Many custom footprints were made with accurate dimensions

according to the actual component and space on the PCB. The physical dimension of the PCB is

45.70 mm x 46.00 mm which meets the requirement from the Robosub club. The requirement of

dimension for the PCB is 56.20 mm x 50.00 mm. The front-copper layer was used for placing all

components and connection tracks between them. The front copper layer was used for all

components and the back-copper layer was used for the names of our clients, professors,

mentors and faculty volunteer. A logo of Robosub club and our team member’s names are placed

on the front-copper layer. The PCB layout of our onboard system is shown in Figure 6.

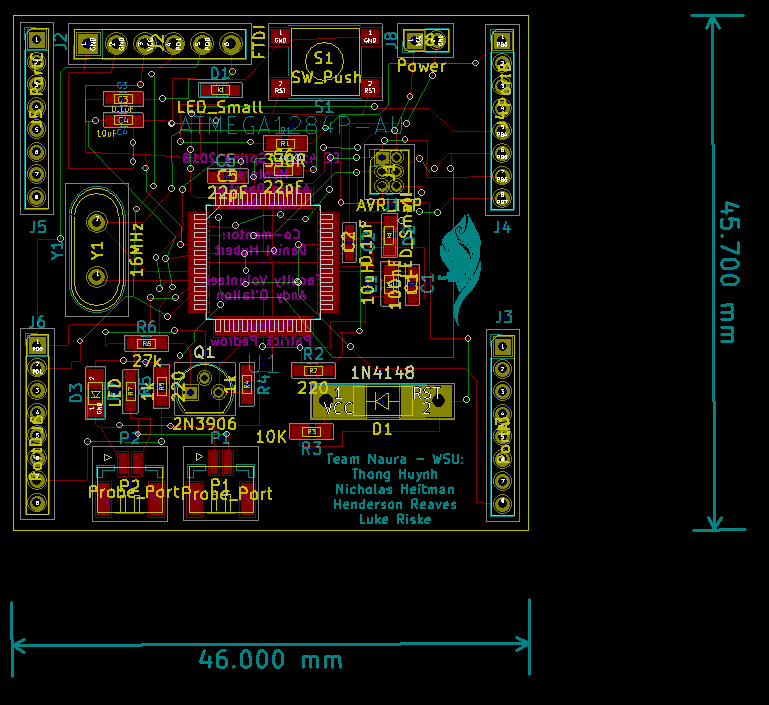
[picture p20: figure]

Fig 6. PCB Layout of the Onboard System

The KiCad software package also provides a 3D viewer that can be used to view our potential

PCB with 3D model formats supported by available 3D plugins. The 3D model of the onboard

PCB is shown with different views in Figure 7 and Figure 8.

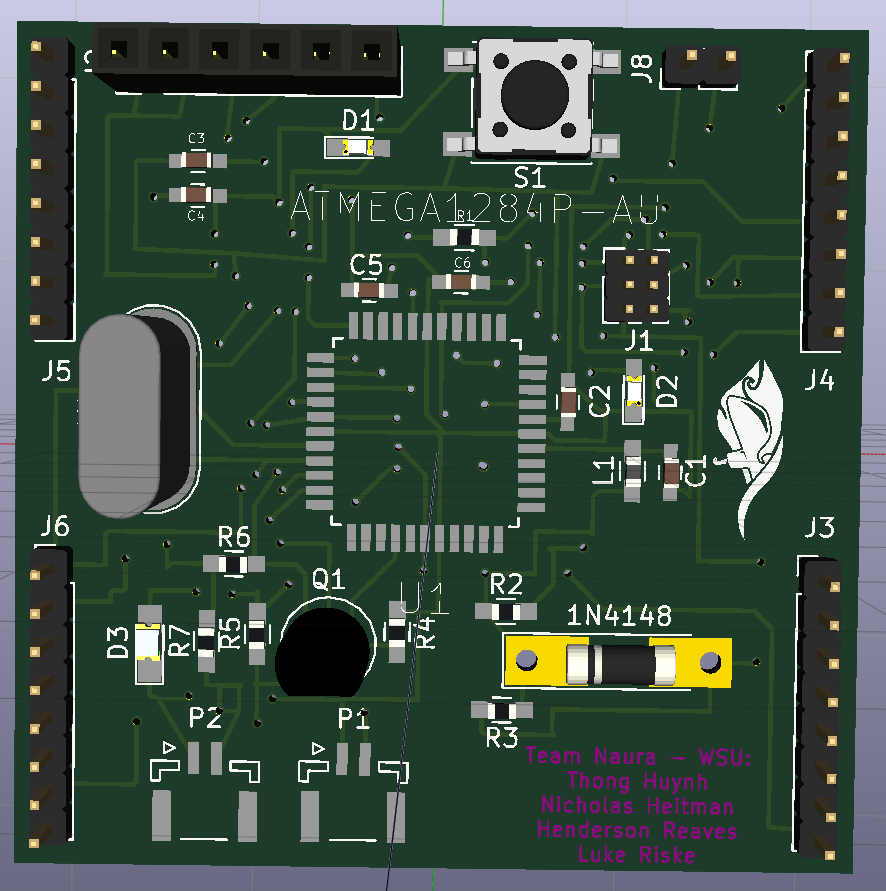
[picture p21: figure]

Fig 7. 3D Model Top View Onboard System PCB

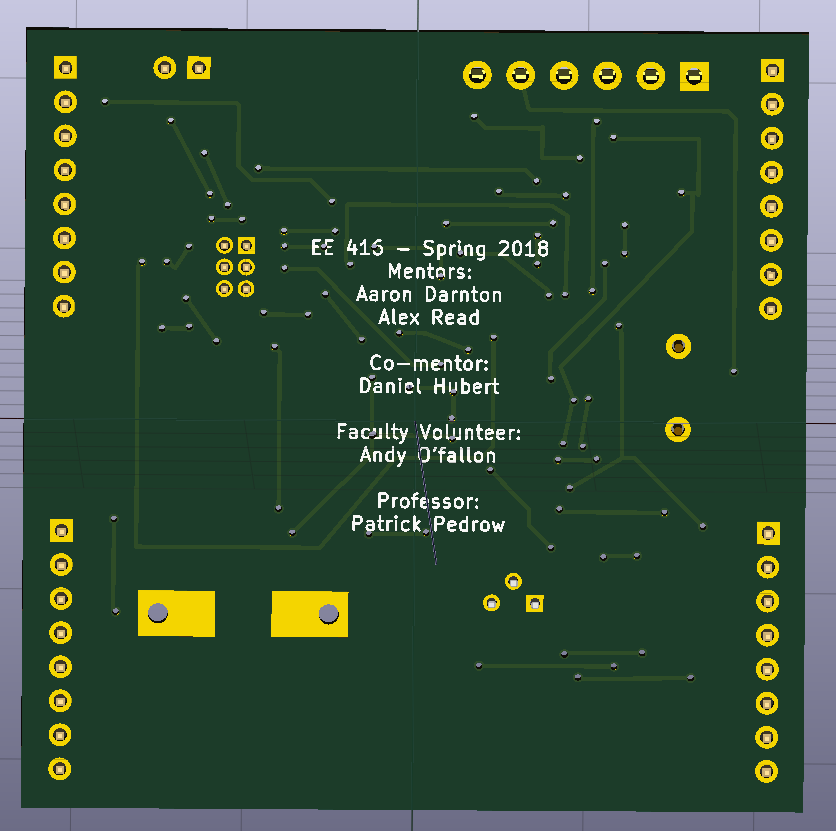
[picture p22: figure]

Fig 8. 3D Model Bottom View Onboard System PCB

In addition, the board is designed with the chip placed in the middle and all components around

it for signal quality purpose. A reset button is added to the board to reset the system if needed.

The probe ports are placed at the end of the board for easy access when the PCB is integrated

on the sub. The JST_GH connection ports with 1.25 mm pitch are used for the probe ports. Since

we use OSH Park as our manufacturer for PCB layouts, we need to follow their design rules for minimum trace widths, trace spacing, drill diameter, and annular ring diameter from OSH Park.

Our PCBs layout meets all of these requirements.

Simulation Results:

Several | simulation tests | were performed for each schematic and PCB design during the design

process to ensure our design meets all client’s requirements with no errors. When the schematic

of the onboard system was designed, the electrical rules check (ERC) application was performed

to make sure all the connections on the schematic were correct. There were no errors or warnings

found during the process. The record of the testing process is shown in Figure 9. In addition, the

design rules check (DRC) was performed for the PCB design to ensure all the design rules were

satisfied. There were no problems or unconnected errors found during the process. The record of

this process is shown in Figure 10.

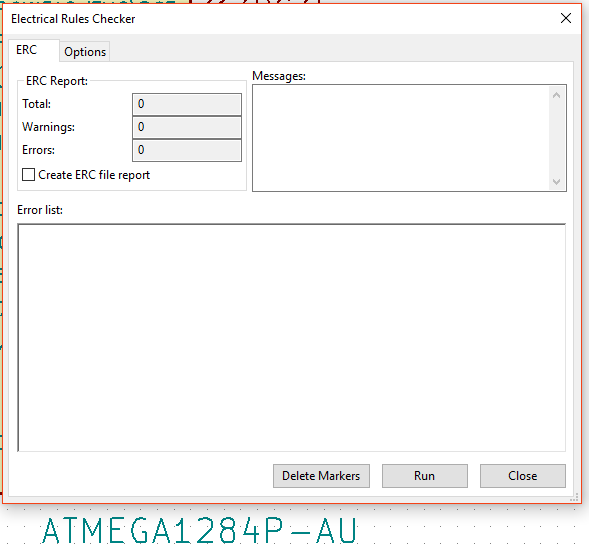
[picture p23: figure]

Fig 9. ERC Testing Process Onboard System PCB

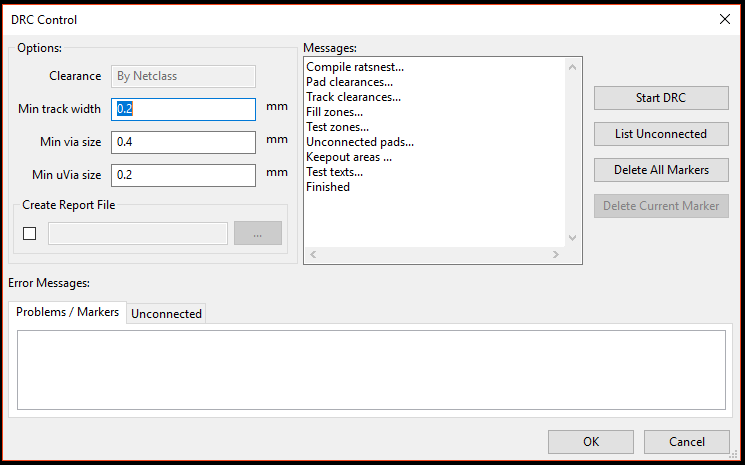
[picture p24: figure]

Fig 10. DRC Check Onboard System PCB

Since the actual board for the PCB design did not arrive in time, the testing process was

constructed on a breadboard with the SOS leak detector, and with Arduino Nano. The Arduino

Nano uses a similar microcontroller to our onboard system. It uses an atmega328P, which has a

smaller amount of memory than our actual microcontroller (atmega1284P). The memory

comparison table for both microcontrollers is shown in Table 2.

Table 2 Memory Comparison Table

Features | Atmega328P | Atmega1284P
Flash (Bytes) | 32K | 128K
SRAM (Bytes) | 2K | 16K
EEFROM (Bytes) | 1K | 4K

However, for this project, we do not need a lot of memory from the chip. Therefore, it will not affect

our testing results. The probe was connected to the Arduino Nano board, and an LED on the

breadboard. The code was written and uploaded to the Arduino Nano via Arduino IDE. When the

probe is dry, the LED will not turn on and a “Dry!” message will be sent to the CPU. When the

probe is wet, the LED will turn on and a “Leak!” messages will be displayed.

The record of the testing process is provided in Figure 11, Figure 12, Figure 13, and Figure 14,

The test was constructed successfully. The analog signal was used to detect the leak and send

warning messages to the CPU. The SOS Leak Sensor was able to detect the leak with one drop

of water and sent the warning message to the CPU. The LED which is used to indicate the sensor

status was turned on when a leak occurs. In addition, when there is no leak, the signal is not

pulled high to the VCC, and the LED will not be turned on. The system also sends a “safe”

message to the CPU in this case.

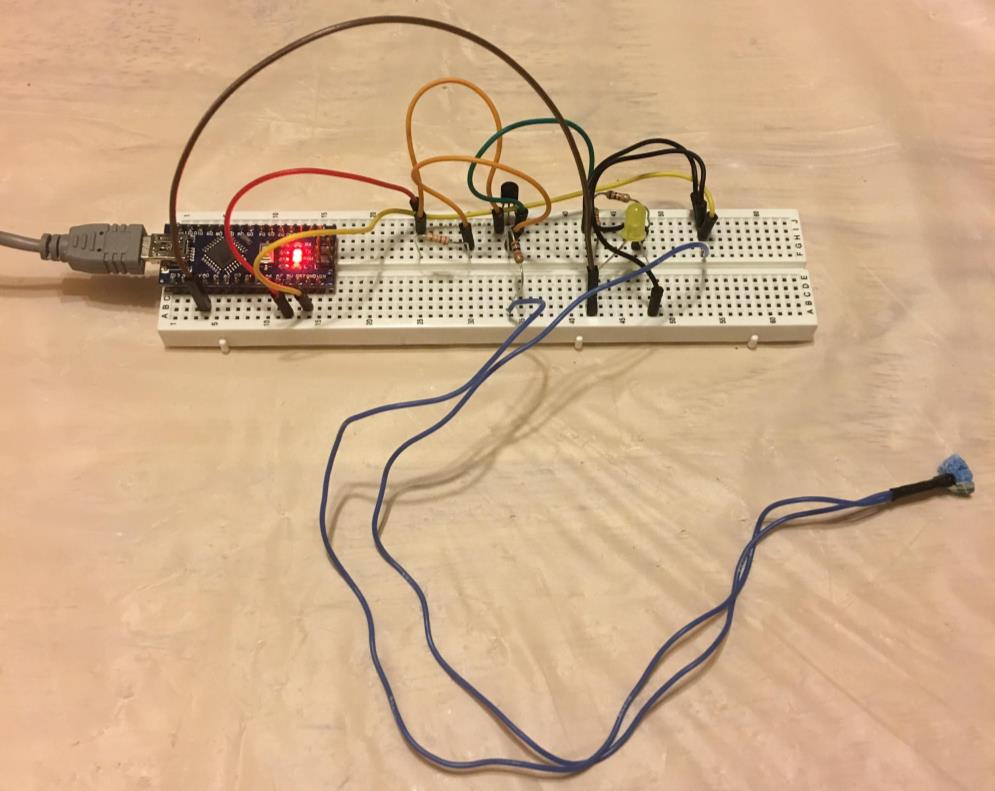
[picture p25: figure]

Fig 11. The Dry Probe With LED Off

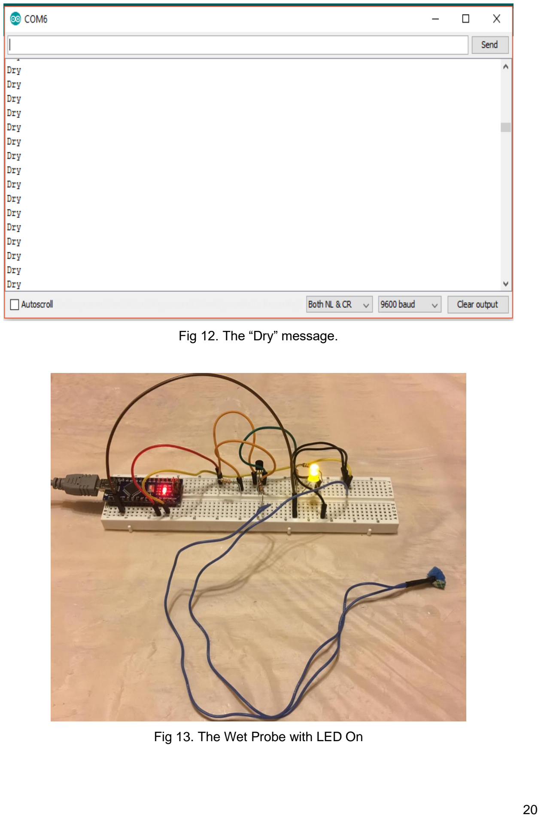
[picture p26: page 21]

Fig 12. The “Dry” message.

Fig 13. The Wet Probe with LED On


Fig 14. The “Leaking” Message

A back up plan was designed in case the onboard system does not work as we expected. The

Arduino Nano Shield was built with the SOS Leak Sensor as the backup plan. Another schematic

and PCB were designed for the Arduino Nano Shield, with the SOS leak sensor. The schematic

of Arduino Nano Shield is designed based on the requirements of this project. The SOS Leak

Sensor is added to the schematic as well as indicator LEDs. The schematic of our backup plan is

shown in Figure 15.


Fig 15. Arduino Nano Shield with SOS Leak Sensor Schematic

The method used to design the Arduino Nano Shield is more simple than the onboard system.

There are three main components on the design, which include: the Arduino Nano shield, SOS

Leak Sensor, and Power Supply. The SOS Leak Sensor is designed the same as the onboard

system. The Power Supply will come from the actual Arduino Nano, and an indicator LED is used

to check the power’s signal. The Arduino Nano Shield is designed with thirty pins, 15 pins on each

side and the dimension of each pin have to match with the pin of actual Arduino Nano which is

0.1 inch. The dimension of the shield needs to be 1.9 inch x 0.8 inch according to the physical

dimension of the Arduino Nano.

Moreover, all the testing processes, electrical rules check, and design rules check were performed

for this design as well. A Robosub club logo is placed on the front-copper layer of the PCB and

our team member names are placed on the back-copper layer of the PCB. layout of Arduino Nano

Shield is shown in Figure 15. The testing results are shown in Figure 17, and Figure 18. No errors were found during this testing process which means all the connections on the schematic are

correct.


Fig 16. The PCB layout of Arduino Nano Shield with SOS Leak Sensor


Fig 17. ERC testing process Arduino Nano Shield

Fig 18. DRC Testing Process Arduino Nano Shield

In addition, an Arduino Nano was used in the breadboard model with SOS Leak Sensors and an

indicator LED to test for prototype. The results satisfy our client’s requirements. Thus, our backup

plan is successfully designed and tested.

Broader Impacts and Contemporary Issues

Underwater vehicles are currently providing strong opportunities on the WSU campus. Current

development of these vehicles is directed towards exploration on Earth and outer space. In the

article, “WSU Researchers Build -300ºF Alien Ocean to Test NASA Outer Space Submarine,”

Tina Hilding describes the current research towards creating a testing chamber to emulate a

submarine exploring the seas of Saturn's moon “Titan.” [3] Having a submarine in this

environment would impact our methods of leak detection immensely. The variable temperatures

and pressure levels of Titan would require our design to be reconsidered from both software and

hardware standpoints. The article “A new generation of Titanic exploration,” by Randy Bolerjack

explains another project currently being pursued on the WSU campus. The article explains WSU

electrical contributions to a five-person submarine with hopes of descending to view the wreckage of the Titanic in the near future. [4] This project could integrate with similar methods of leak

detection we developed throughout this course. Reconsiderations would have to be made to

account for size of the submarine, and level of pressures experienced at the depths of the Titanic.

The future for autonomous vehicles is promising. Autonomous vehicles have already been

introduced to society in the form of drones and driverless cars, where innovation is still taking

place. However, Autonomous Underwater Vehicles (AUVs) are still in the early stages because

they face a big barrier, water. The underwater environment that these vehicles operate in blocks

all electromagnetic radiation waves which is what all other conventional communication systems

use, hence the need for new innovations. Despite this fact there are a lot of commercial and

military applications for these vehicles. The article titled “Infographic: The Future of Autonomous

Underwater Vehicles” by Stephen Cass provides some details on how AUVs have adapted over

the past 10 years to overcome some of the design challenges posed by the aquatic environment.

For example, when inspecting underwater infrastructure such as pipelines, they could use a

combination of sonar and camera systems to identify landmarks on the seafloor for reference. [5]

In recent years, the concept of networking has become popular between underwater autonomous

vehicles. The article “Low Cost Autonomous Underwater Vehicles for New Concepts of Coastal

Field Studies,” by L. Madureiraf, A. Sousaf, J. Sousa and G. Goncalves provides benefits to

networking vehicles for environmental studies. When referring to acquisition of data during the

event of a natural disaster they write, “With the current technologies, tools, and models, it is simply

not possible to inter-operate vehicles, sensors and communication networks with different

vendors/institutions” (Madureiraf, 2009). They infer that networking autonomous vehicles can

spread information more effectively, but this function in autonomous vehicle manufacturing is

limited. The authors also explain that networking provides the opportunity for better planning, and

supervision of underwater missions from land. [6]

In their current state Autonomous Underwater Vehicles are widely used throughout the

Oceanography field to gather data and perform certain tasks for researchers. However, some

suggest that they are not as effective as they could be. The article titled “Adaptive Autonomous

Underwater Vehicles: An Assessment of Their Effectiveness for Oceanographic Applications” by

Mario Paulo Brito and other contributors, explains how AUVs are behaving more automatic than

autonomous, meaning their behavior isn’t as adaptive as it could be which leaves more exciting

data ungathered. The main difference here is that adaptive mission planning (AMP) isn’t being utilized by the AUVs in the field. Of all the researchers surveyed agree that the scarcity of

demonstration trials for AMP on AUVs is a primary cause for this difference in operation. If these

trials could be conducted the possibilities would greatly increase. [7]

Limitations and Recommendations

There are three major limitations that have been assessed with the pre-submersion beta prototype

system. These limitations deal with component reposition on the PCB, and space constraints of

the portable case.

One of the limitations of the pre-submersion leak detection system is the current orientation of the

LCD screen. The portable case was designed with the LCD screen mounted upside down when

propped in the upright position, which makes it difficult for the user to determine the state of the

test. The current orientation of the LCD screen when the case is in the upright position is shown

in Figure 18. Our team tried to mitigate this problem with software revisions by printing characters

to the LCD upside down, but only 8 custom characters are available to be produced out of 32

total. This has since been fixed in the PCB layout, and it is recommended that the Robosub club

uses the revised layout if it is ever reprinted. This could also be fixed by reprinting the portable

case with the mounting position in the opposite direction. It is still possible to easily visualize the

state of the test when the case is placed with the window facing upward.


Fig. 18 LCD Screen with Upside Down Orientation

In addition, the layout of the pre-submersion PCB was made with the barrel jack port facing inward

by mistake. Luckily, the port still plugs in, but it would be convenient to be plugged in from the

outward position. The picture in Figure 19 shows the barrel jack port facing inward to the PCB.

This limitation has been revised in the PCB layout, which is recommended if the PCB needs to

be reprinted in the future.


Fig. 19 Inward Orientation of the Barrel Jack Adapter

The biggest limitation of our pre-submersion system is the strength of the vacuum generator.

From our testing results, it takes an average of 46.1s to reach the threshold of 0.9ATM when used

with the Robosub autonomous submarine. If the current testing time is undesirable, this vacuum

operation time could be decreased substantially with a more powerful vacuum. Although, if

replaced, the size of the portable case must be considered. The portable case only supports the

footprint of the current vacuum generator, and we recommend that it is revised if the vacuum is

ever substituted.

Conclusions and Future Work

Overall, the current state of the pre-submersion system is a functional beta prototype. Our test

results conclude that the system is capable of testing airtightness on a closed vessel. Over the

course of this semester the pre-submersion system has been developed into a simplistic

standalone unit that can be used to test multiple vessels. To further enhance the system will

require layout revisions to be reprinted, and modifications to the portable case. These limitations

will require extra time, and budgeting moving forward. The system functions as desired in the

current state, and it is up to the client if future work needs to be poured into these revisions.

From our test results, the onboard system performs as intended. The system still requires

integration with the Robosub autonomous submarine. This will be considered as future work for

the final weeks of the semester.

Acknowledgements

The following people provided us with help, and guidance throughout the course of the semester:

I. Aaron Darnton and Alex Reed - NAVSEA Mentors
II. | Professor Andrew O’fallon - Faculty Mentor
III. | Ben Songras - WSU Robosub Club Electrical Engineer Leader
IV. | Ryan Summers - Robosub Club Leader
V. Alex Lanphere - Portable Case Designer for Pre-Submersion System
VI. | Rustom Jehangir - Employee at Blue Robotics (permitted use of the circuit to read SOS
| probes)

References

[1] Atmel, “8-bit AVR Microcontroller,” Atmega1284P datasheet, Oct. 2016
[2] “Thrusters & Motors.” SOS Leak Sensor Documentation, docs.bluerobotics.com/sos/.
[3] | Hilding, T. | (2018, February 08). WSU researchers build -300ºF alien ocean to test NASA
outer space submarine | WSU Insider | Washington State University. Retrieved April 16, 2018,

from https://news.wsu.edu/2018/02/07/wsu-builds-nasa-alien-ocean/

[4] Bolerjack, R. (2018, February 21). A new generation of Titanic exploration | WSU Insider
| | Washington | State | University. | Retrieved | April | 16, | 2018, | from

https://insider.wsu.edu/2018/02/21/a-new-generation-of-titanic-exploration/

[5] Cass, S. (2016, June 27). Infographic: The Future of Autonomous Underwater Vehicles.

Piscataway, NJ, Institute of Electrical and Electronics Engineers Retrieved April 16, 2018, from

https://spectrum.ieee.org/static/infographic-the-future-of-autonomous-underwater-vehicles

[6] Madureira, L., Sousa, A., Sousa, J., & Gonçalves, G. (2009). Low Cost Autonomous

Underwater Vehicles for New Concepts of Coastal Field Studies. Journal of Coastal Research,

238-242. Retrieved from http://www.jstor.org/stable/25737573

[7] M. P. Brito, R. S. Lewis, N. Bose and G. Griffiths, "Adaptive Autonomous Underwater

Vehicles: An Assessment of Their Effectiveness for Oceanographic Applications," in IEEE

Transactions on Engineering Management.

doi: 10.1109/TEM.2018.2805159

URL: http://ieeexplore.ieee.org/stamp/stamp.jsp?tp=&arnumber=8318894&isnumber=4429834

Appendix

Appendix A. Team Photo


Left to Right: Thong Huynh, Henderson Reaves, Nick Heitman, Luke Riske

Appendix B. Description of EE415 Senior Design Algorithm

In EE415 we were asked to design a leak detection system for the WSU Robosub club. After

labeling the customer needs, we began our pursuit of target specifications. We were informed

that the club wanted the system to be: a standalone system that operated on its own power source, simple in design so that it could be removed during maintenance work, arduino

compatible, and able to check the pressure of the system pre submersion. Moving forward we

began to develop concepts.

The concepts we came up with included: building a small robot to patch leaks if they occurred, a

moisture detection system similar to those in commercial optical fiber cables, and using a

pressure sensor to detect deviations in pressure that would indicate a leak. Originally, we had

decided to pursue the pressure sensor method, and began brainstorming for that particular

design. After being advised by our mentor Aaron Darnton that pressure deviations would not be

great enough to signify a leak, we decided to go with the moisture detection method. At this point

in time it was brought to our attention that this project should consist of two separate designs: the

onboard system to detect water infiltration, and an off board pre-submersion pressure system that

would be automated.

Putting the onboard system on hold, we started the iterative design process over, and began to

work on the automated vacuum system. We knew what the club wanted so we got started on

establishing target specifications. The club said that they wanted the internal pressure to be

brought down to 0.9ATM, and that it should hold this pressure over a substantial amount of time.

Knowing the target specifications we began the concept generation process.

To simplify our concept generation process we started by making sure we did not encroach on

any designs that have been patented, so we researched the Thomas register, and patents in this

field of work. A vacuum generator, a pressure sensor, an arduino compatible chip were the

baseline for the project. We were informed by our mentor Aaron Darnton that the vacuum

generator could be an air mattress pump, but the club had already come into contact with a

vacuum generator. We decided to utilize the one that the Robosub club provided. We then began

brainstorming the functional process for the system, and determined which concepts we would

actually select.

Utilizing a concept selection table we broke down every area that our system would need to cover

in order to function, and began researching components that fit the target specifications. After

assembling a list for all of the component that would be required for the project to function

correctly, we began designing multiple layout configurations, for which the project could be built.

Next we selected, and constructed the project on a breadboard. Then we tested its functionality, and began to plan for the future Beta Prototype development, and how we could potentially

improve the system we had just created.

At the end of EE415 we had a fully functional alpha prototype for the pre-submersion system of

leak detection. Moving into EE416 we knew that we still needed to develop the onboard system

to fully satisfy the clients needs. Our team also wanted to simultaneously shift our pre-submersion

alpha prototype to a PCB, and simplify the mass of wires we had in its the breadboard circuit. We

also wanted to provide a portable carrying case so that all of the pre-submersion components

were contained, and easily transportable.

Appendix C. Images of Portable Case for Pre-Submersion System (Accredited to Alex

Lanphere)


C-1: 3-D Model Exploded View of Portable Case for Pre-Submersion System


C-2: Back View of Portable Case for Pre-Submersion System


C-3: Front View of Portable Case for Pre-Submersion System

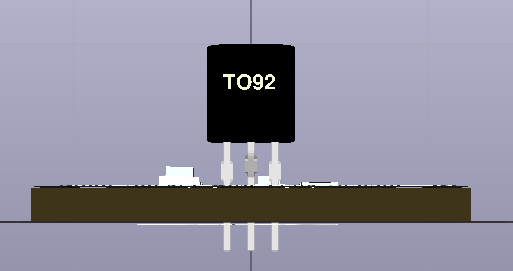
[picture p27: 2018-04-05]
Arduino_Nano_Shield_pics/3D_front.PNG

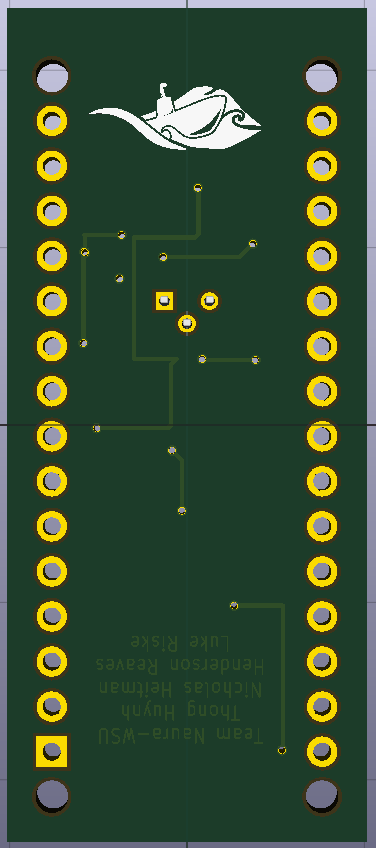
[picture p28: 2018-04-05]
Arduino_Nano_Shield_pics/3D_bottom.PNG

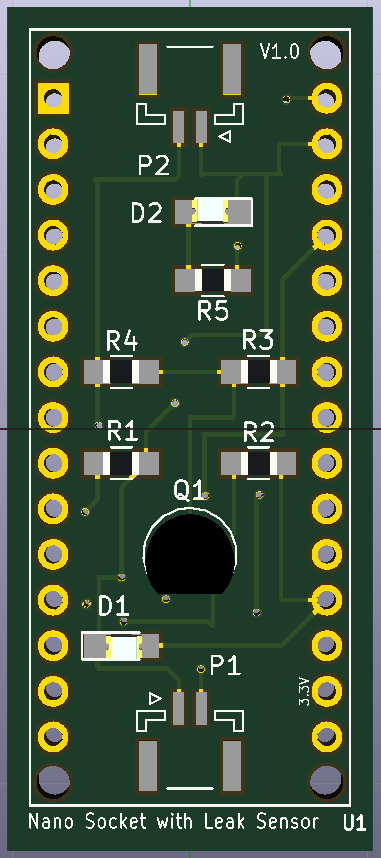
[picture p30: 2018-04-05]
Arduino_Nano_Shield_pics/3D_top.PNG

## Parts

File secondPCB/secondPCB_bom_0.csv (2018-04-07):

Component | Description | Part | References | Value | Footprint | Quantity Per PCB | Datasheet | Digikey
1 | Diode | D | 1N4148 | D1 | D_MELF-RM10_Universal_Handsoldering | 1 |  | 1N4148FS-ND
2 | Unpolarized capacitor | C | C1 C2 C4 | 100nF | C_0603_HandSoldering | 10 |  | 445-5201-1-ND
3 | Unpolarized capacitor | C | C3 | 10uF | C_0603_HandSoldering | 10 |  | 490-12317-1-ND
4 | Unpolarized capacitor | C | C5 C6 | 22pF | C_0603_HandSoldering | 10 |  | 399-9030-1-ND
5 | LED generic | LED | D3 | LED | LED_0805_HandSoldering | 1
6 | LED, small symbol | LED_Small | D1 D2 | LED_Small | LED_0603_HandSoldering | 10 |  | 160-1448-1-ND
7 |  | AVR_ISP | J1 | AVR_ISP | Pin_Header_Straight_2x03_Pitch1.27mm | 5 |  | S9015E-03-ND
8 | Generic connector, single row, 01x02 | Conn_01x02 | J8 | Conn_01x02 | Pin_Header_Straight_1x02_Pitch2.00mm | 2 |  | S5800-02-ND
9 |  | FTDI-RESCUE-secondPCB | J2 | FTDI | Socket_Strip_Straight_1x06_Pitch2.54mm | 10 |  | S7039-ND
10 |  | PortA | J3 | PortA | Pin_Header_Straight_1x08_Pitch2.00mm | 4 |  | S5751-08-ND
11 |  | PortB | J4 | PortB | Pin_Header_Straight_1x08_Pitch2.00mm | 4 |  | S5751-08-ND
12 |  | PortC | J5 | PortC | Pin_Header_Straight_1x08_Pitch2.00mm | 1 |  | S5751-08-ND
13 |  | PortD | J6 | PortD | Pin_Header_Straight_1x08_Pitch2.00mm | 1 |  | S5751-08-ND
14 | Inductor | L | L1 | 10uH | L_0603_HandSoldering | 10 |  | 587-1714-1-ND
15 |  | Probe_Port | P1 P2 | Probe_Port | JST_GH_SM02B-GHS-TB_02x1.25mm_Angled | 4 |  | 455-1564-1-ND
16 | -40V Vce, -0.2A Ic, PNP, Small Signal Transistor, TO-92 | 2N3906 | Q1 | 2N3906 | TO-92_Molded_Narrow | 2 | https://www.fairchildsemi.com/datasheets/2N/2N3906.pdf | 2N3906CS-ND
17 | Resistor | R | R3 | 10K | R_0603_HandSoldering | 10 |  | P20397CT-ND
18 | Resistor | R | R4 R7 | 1k | R_0603_HandSoldering | 10 |  | RHM1.0KDCT-ND
19 | Resistor | R | R2 R5 | 220 | R_0603_HandSoldering | 10 |  | RHM220DCT-ND
20 | Resistor | R | R6 | 27k | R_0603_HandSoldering | 10 |  | RHM27.0KADCT-ND
21 | Resistor | R | R1 | 330R | R_0603_HandSoldering | 10 |  | RHM330DCT-ND
22 | Push button switch, generic, two pins | SW_Push | S1 | SW_Push | SW_SPST_PTS645 | 10 |  | CKN9088CT-ND
23 |  | ATMEGA1284P-AU-RESCUE-secondPCB | U1 | ATMEGA1284P-AU | QFP80P1200X1200X120-44N | 2 |  | ATMEGA1284P-AU-ND
24 | Two pin crystal | Crystal | Y1 | 16MHz | Crystal_HC49-4H_Vertical | 10 |  | XC1748-ND
Component Groups: | 24
Component Count: | 31
Fitted Components: | 31
Number of PCBs: | 1
Total components: | 31
Schematic Version: | 0
Schematic Date: | 3/25/2018
BoM Date: | 4/7/2018 1:56
Schematic Source: | C:\Users\Thong_Huynh\Desktop\secondPCB\secondPCB.sch
KiCad Version: | Eeschema 4.0.7

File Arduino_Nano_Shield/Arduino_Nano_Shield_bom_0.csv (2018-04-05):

Component | Description | Part | References | Value | Footprint | Quantity Per PCB | Datasheet | Digikey
1 | LED generic | LED | D1 D2 | LED | LED_0805_HandSoldering | 4 |  | L62501CT-ND; 1516-1085-1-ND
2 |  | Probe_Port | P1 P2 | Probe_Port | JST_GH_SM02B-GHS-TB_02x1.25mm_Angled | 6 |  | 455-1564-1-ND
3 | -40V Vce, -0.2A Ic, PNP, Small Signal Transistor, TO-92 | 2N3906 | Q1 | 2N3906 | TO-92_Molded_Narrow | 2 | https://www.fairchildsemi.com/datasheets/2N/2N3906.pdf | 2N3906CS-ND
4 | Resistor | R | R1 R4 | 1K | R_0805_HandSoldering | 10 |  | P1.0KDACT-ND
5 | Resistor | R | R2 R5 | 220 | R_0805_HandSoldering | 10 |  | 408-1779-1-ND
6 | Resistor | R | R3 | 27K | R_0805_HandSoldering | 10 |  | P27KDACT-ND
7 |  | Arduino_Nano_Socket | U1 | Arduino_Nano_Socket | Arduino_Nano_Socket | 2 |  | S7013-ND
Component Groups: | 7
Component Count: | 11
Fitted Components: | 11
Number of PCBs: | 1
Total components: | 11
Schematic Version: | 0
Schematic Date: | 3/25/2018
BoM Date: | 4/4/2018 23:13
Schematic Source: | C:\Users\Thong_Huynh\Desktop\EE 416_new\Arduino_Nano_Shield\Arduino_Nano_Shield.sch
KiCad Version: | Eeschema 4.0.7

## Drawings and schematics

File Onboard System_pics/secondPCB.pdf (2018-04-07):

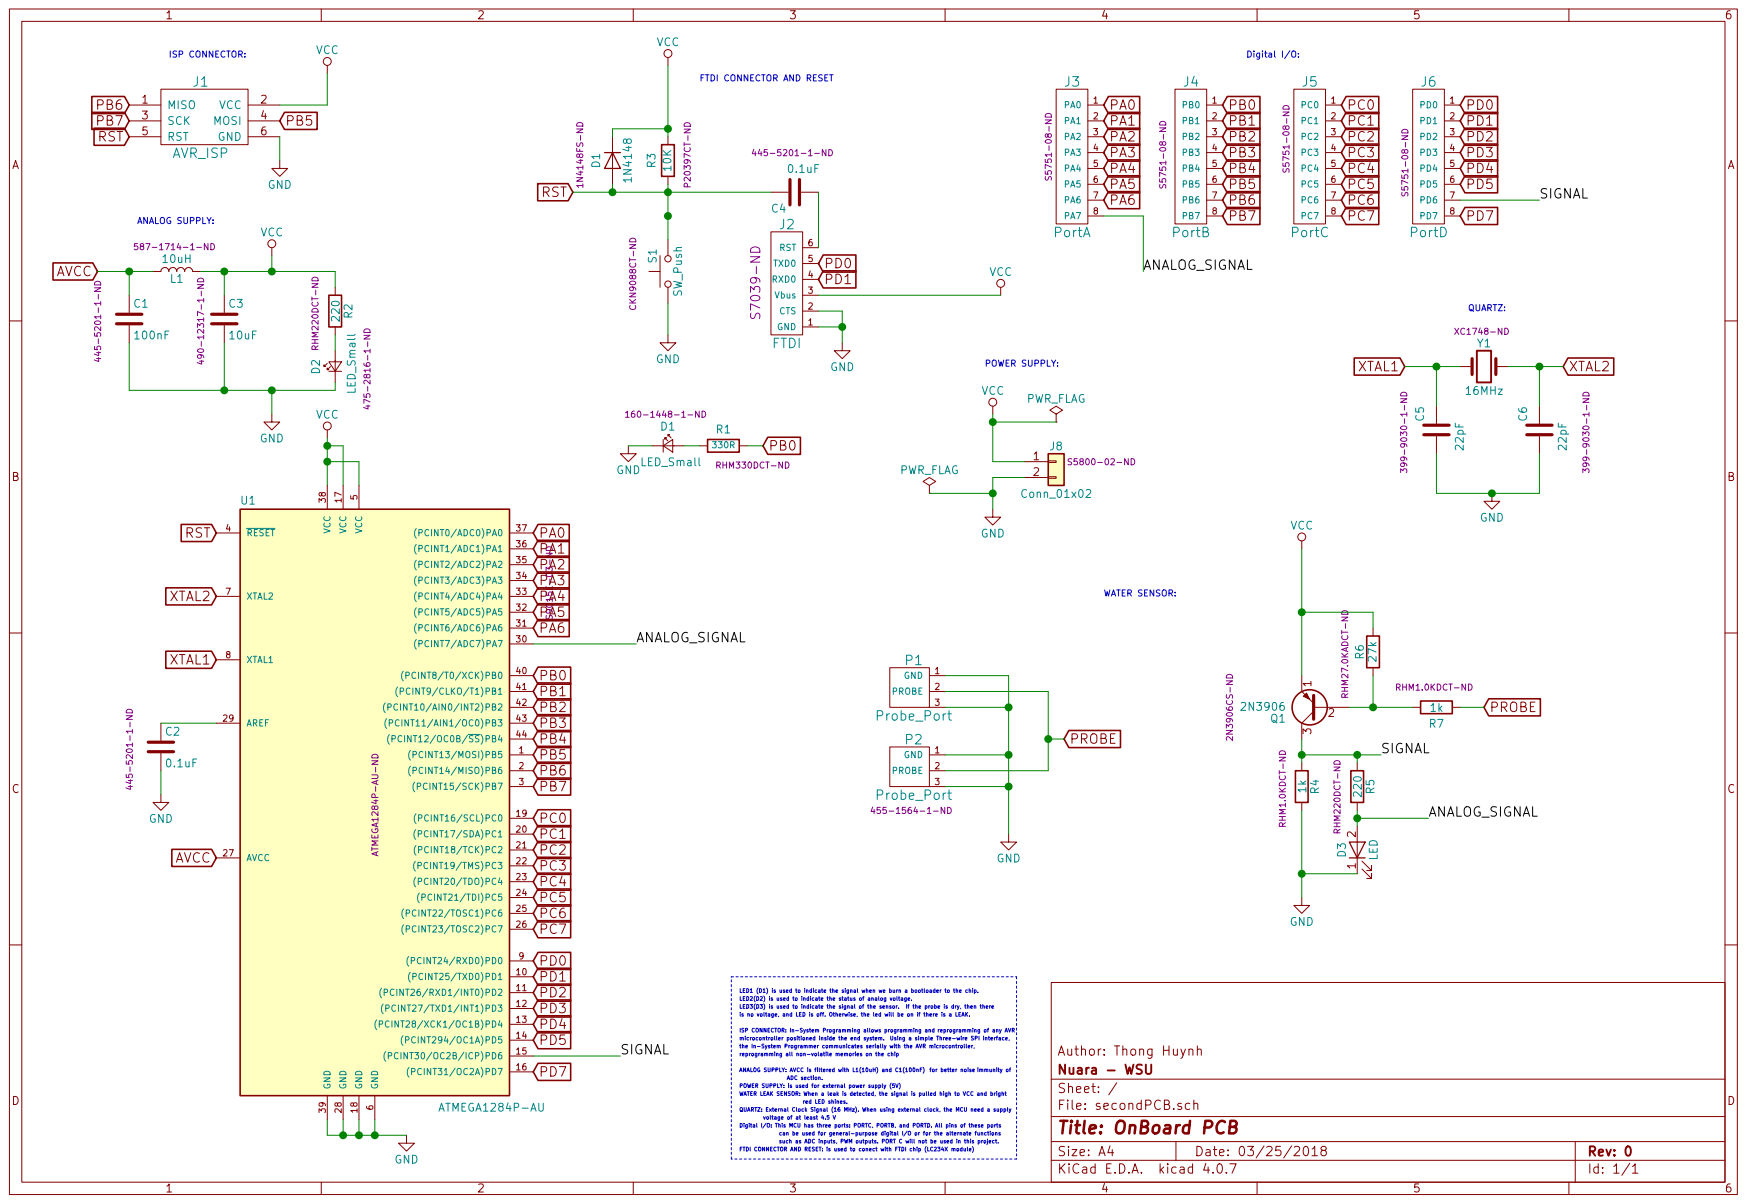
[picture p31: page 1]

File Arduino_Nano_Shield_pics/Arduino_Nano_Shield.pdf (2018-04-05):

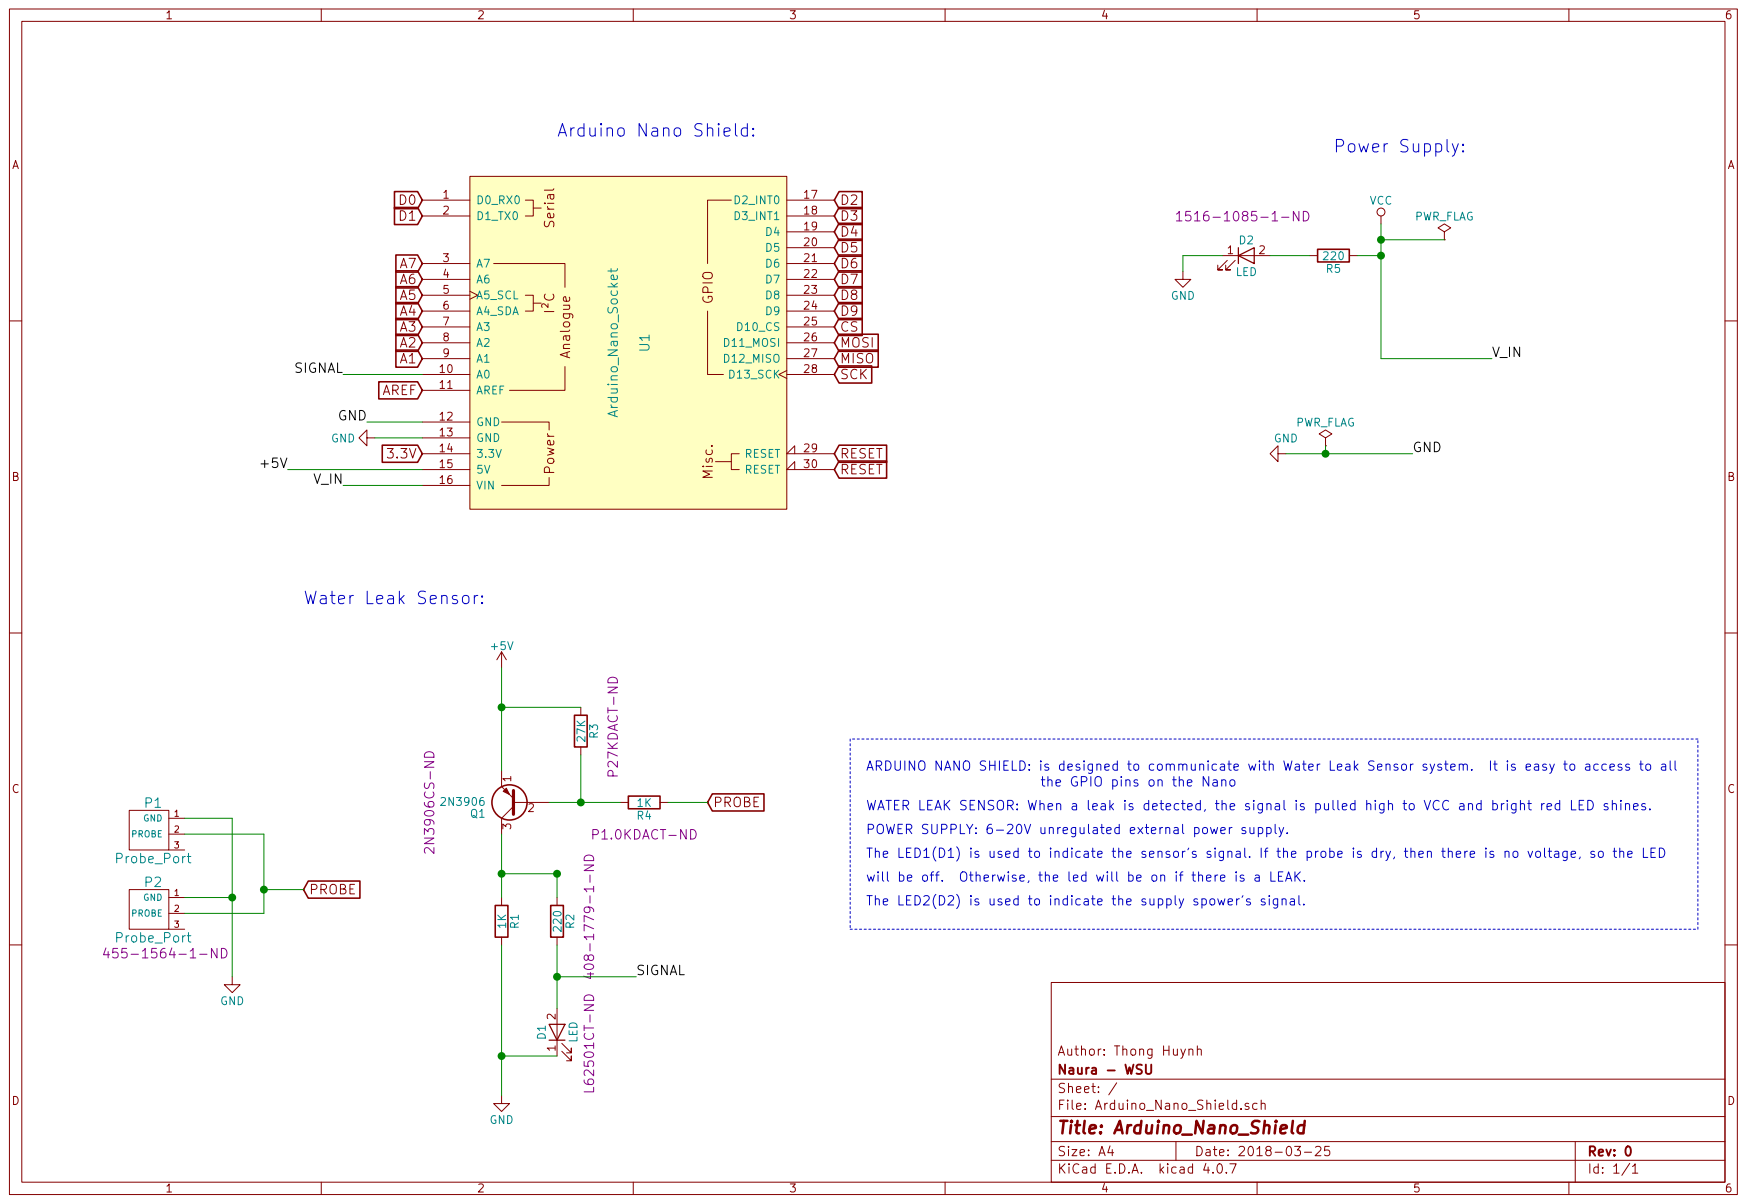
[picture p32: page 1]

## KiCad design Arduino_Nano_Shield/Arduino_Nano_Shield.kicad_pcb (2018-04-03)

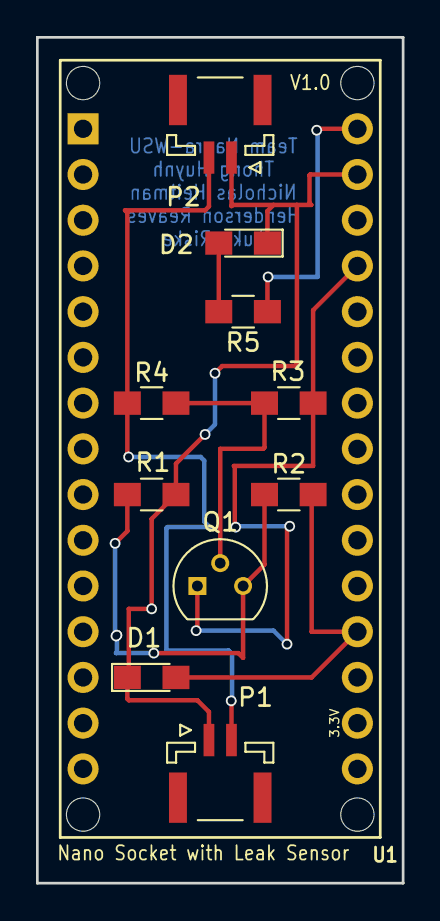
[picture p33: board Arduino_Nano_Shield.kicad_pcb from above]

Board: 2 copper layers, 20.3 x 47.0 mm, 11 parts (0 on the bottom side), 8 nets.

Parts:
D1, D2: LED; LED_0805_HandSoldering
P1, P2: Probe_Port; JST_GH_SM02B-GHS-TB_02x1.25mm_Angled
Q1: 2N3906; TO-92_Molded_Narrow
R1, R4: 1K; R_0805_HandSoldering
R2, R5: 220; R_0805_HandSoldering
R3: 27K; R_0805_HandSoldering
U1: Arduino_Nano_Socket

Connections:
+5V: Q1.1, R3.1, U1.5V
/SIGNAL: D1.2, R2.2, U1.A0
GND: D1.1, D2.1, P1.1, P2.1, R1.2, U1.GND2
unnamed: D2.2, R5.2
unnamed: Q1.2, R3.2, R4.2
unnamed: Q1.3, R1.1, R2.1
PROBE: P1.2, P2.2, R4.1
VCC: R5.1, U1.VIN

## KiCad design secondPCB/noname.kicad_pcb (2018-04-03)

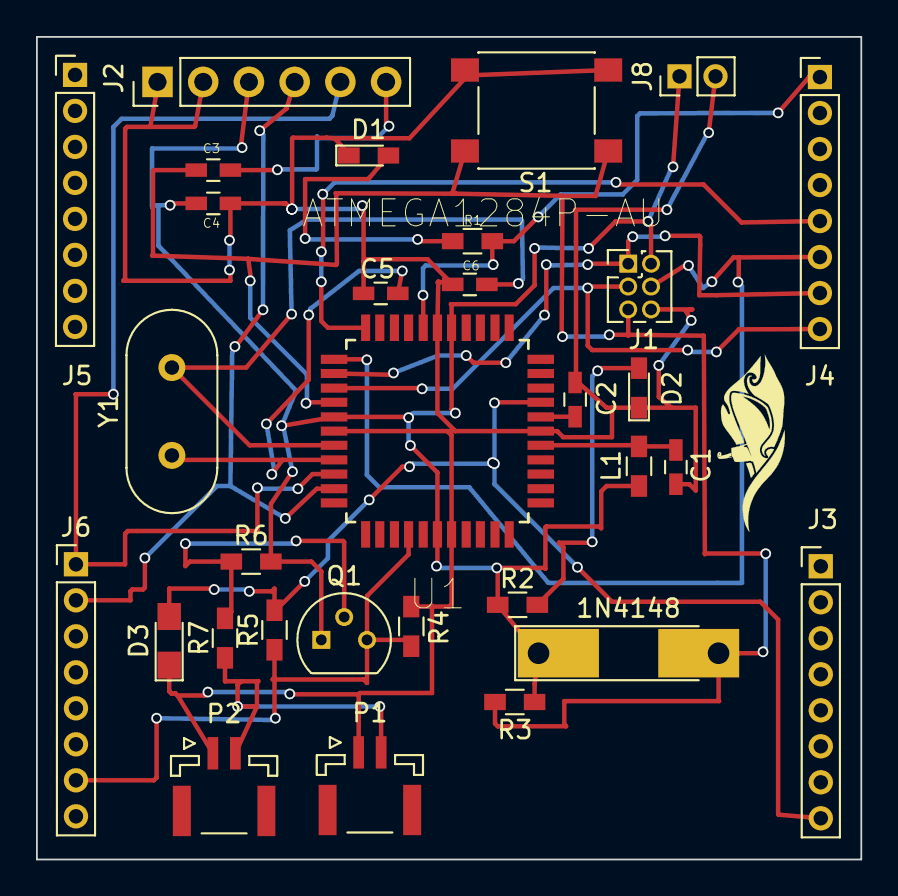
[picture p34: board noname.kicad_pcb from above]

Board: 2 copper layers, 45.8 x 45.7 mm, 31 parts (0 on the bottom side), 21 nets.

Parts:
1N4148: D1; D_MELF-RM10_Universal_Handsoldering
C1: 100nF; C_0603_HandSoldering
C2, C4: 0.1uF; C_0603_HandSoldering
C3: 10uF; C_0603_HandSoldering
C5, C6: 22pF; C_0603_HandSoldering
D1, D2: LED_Small; LED_0603_HandSoldering
D3: LED; LED_0805_HandSoldering
J1: AVR_ISP; Pin_Header_Straight_2x03_Pitch1.27mm
J2: FTDI; Socket_Strip_Straight_1x06_Pitch2.54mm
J3: PortA; Pin_Header_Straight_1x08_Pitch2.00mm
J4: PortB; Pin_Header_Straight_1x08_Pitch2.00mm
J5: PortC; Pin_Header_Straight_1x08_Pitch2.00mm
J6: PortD; Pin_Header_Straight_1x08_Pitch2.00mm
J8: Power; Pin_Header_Straight_1x02_Pitch2.00mm
L1: 10uH; L_0603_HandSoldering
P1, P2: Probe_Port; JST_GH_SM02B-GHS-TB_02x1.25mm_Angled
Q1: 2N3906; TO-92_Molded_Narrow
R1: 330R; R_0603_HandSoldering
R2, R5: 220; R_0603_HandSoldering
R3: 10K; R_0603_HandSoldering
R4, R7: 1k; R_0603_HandSoldering
R6: 27k; R_0603_HandSoldering
S1: SW_Push; SW_SPST_PTS645
U1: ATMEGA1284P-AU; QFP80P1200X1200X120-44N
Y1: 16MHz; Crystal_HC49-U_Vertical

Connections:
/ANALOG_SIGNAL: D3.2, J3.8, R5.2, U1.30
/SIGNAL: J6.7, Q1.3, R4.1, R5.1, U1.15
AVCC: C1.1, L1.1, U1.27
GND: C1.2, C2.2, C3.2, C5.1, C6.1, D1.1, D2.1, D3.1, J1.6, J2.1, J2.2, J8.2, P1.1, P2.1, R4.2, S1.1, U1.6, U1.18, U1.28, U1.39
unnamed: C2.1, U1.29
unnamed: C4.1, J2.6
unnamed: D1.2, R1.1
unnamed: D2.2, R2.2
unnamed: Q1.2, R6.1, R7.2
PB0: J4.1, R1.2, U1.40
PB4: J4.5, U1.44
PB5: J1.4, J4.6, U1.1
PB6: J1.1, J4.7, U1.2
PB7: J1.3, J4.8, U1.3
PD0: J2.5, J6.1, U1.9
PD1: J2.4, J6.2, U1.10
PROBE: P1.2, P2.2, R7.1
RST: 1N4148.2, C4.2, J1.5, R3.1, S1.2, U1.4
VCC: 1N4148.1, C3.1, J1.2, J2.3, J8.1, L1.2, Q1.1, R2.1, R3.2, R6.2, U1.5, U1.17, U1.38
XTAL1: C5.2, U1.8, Y1.1
XTAL2: C6.2, U1.7, Y1.2

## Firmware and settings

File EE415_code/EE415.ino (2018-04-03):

// need to check to display message correctly when press >0.935, etc
// Transfer function: 10% to 90% of Vsupply (analog), 2^14 count (digital)




// check to see if we need 1 byte or 2 bytes for the data from sensor to MCU


// Combined the Sensor_reading function to main?


// Check with Arduino 1.6.8 for the plotter -> modify the source file to change the scale?


// updated pin for power replay



#include <SPI.h> // Using SPI library


#include <Arduino.h> // Using Arduino library


#define p_min -15 // Operating pressure is +/- 15 psi


#define p_max 15 // Operating pressure is +/- 15 psi


#define output_min 1638.4 // 1638 counts (10% of 2^14 counts or 0x0666) in digital output


#define output_max 14745.6 // 14745 counts (90% of 2^14 counts or 0x3999) in digital output


#include <LiquidCrystal.h> // LCD library


LiquidCrystal lcd(8, 7, 5, 4, 3, 6); // pin to display the result on lcd


uint8_t SS_pin = 10; // Assign pin for SS line


int off = 0;


int number = 0;


int failed = 0;



void setup() {


  delay(1500);


  Serial.begin(9600); // Serial data transmission: 9600 bits per second -> Lower


  //while(!Serial)


  //{


  //; //Initialize Serial


  //}


  SPI.begin(); // Start the SPI library


  pinMode(SS_pin, OUTPUT); // Initialize the chip select pin


  digitalWrite(SS_pin, HIGH); // Set the digital pin 10 on (5 V)


  pinMode(2, OUTPUT);


  digitalWrite(2, HIGH);


  lcd.begin(16, 2); // Initializes the size of LCD screen


  lcd.clear(); // Clear everything before start


  lcd.print("Pres = "); // Display character


}


void loop()


{



  float get_reading = Sensor_reading(SS_pin);


  // formula to calculate pressure value


  float pressure_psi = (get_reading - output_min) * (p_max - p_min) / (output_max - output_min) + p_min; //Output in psi


  float pressure_psi2 = 14.696 + pressure_psi;


  float ATM_conv = ((pressure_psi) * (1 / 14.696)) + 1; // Convert psi to ATM


  Serial.println(pressure_psi2);


  //Serial.print(" ");


  lcd.setCursor(7, 0);


  lcd.print(ATM_conv);


  lcd.print(" ATM");

  //turn off vacuum


  if (ATM_conv <= 0.8) //Actually 0.9ATM, vacuum releases 0.1ATM of pressure when turned off


  {

    digitalWrite(2, LOW);

    off = 1;

  }

  //testing

  if (off == 1)

  {

    if (ATM_conv >= .935)

    {

      failed = 1;

    }
    number++;

  }

  if (number > 18000)


  {


    if (failed == 1) //failed, output failed message


    {


      lcd.setCursor(7, 1);


      lcd.print("FAILED ");


    }


    else //passed, output passed message


    {


      lcd.setCursor(7, 1);


      lcd.print("PASSED ");


    }


  }


  else


  {


    lcd.setCursor(7, 1);


    lcd.print("TESTING");


  }



}



int16_t Sensor_reading (int8_t SS_pin) {






  SPI.beginTransaction(SPISettings(800000, MSBFIRST, SPI_MODE1)); // Max frequency = 800KHz


  digitalWrite(SS_pin, LOW);






  int Byte1 = SPI.transfer(0x00); // First pressure sensor byte


  int Byte2 = SPI.transfer(0x00); // Second pressure sensor byte






  digitalWrite(SS_pin, HIGH); //SS pin high


  SPI.endTransaction();






  int16_t sensor_output = Byte1 << 8 | Byte2; //Required for shifting first byte left






  return sensor_output; //Return output pressure reading


}

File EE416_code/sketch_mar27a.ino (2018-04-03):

void setup() {
  // initialize serial communication at 9600 bits per second:
  Serial.begin(9600);
}

// the loop routine runs over and over again forever:
void loop() {
  // read the input on analog pin 0:
  int sensorValue = analogRead(A0);
  // Convert the analog reading (which goes from 0 - 1023) to a voltage (0 - 5V):
  float voltage = sensorValue * (5.0 / 1023.0);

if (voltage > 1.0){
  
  Serial.println("LEAK!");  
  }
  else {
    Serial.println("Dry");
    }

  
  // print out the value you read:
  //Serial.println(voltage);
}

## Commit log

2018-04-03 Create Arduino Nano Shield
2018-04-03 Add files via upload
    FTDI - USB connector
